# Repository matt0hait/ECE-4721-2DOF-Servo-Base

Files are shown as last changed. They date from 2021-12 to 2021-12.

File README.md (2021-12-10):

# ECE-4721 2 DOF Servo Base

by Matthew Hait

## Introduction

This project is for ECE-4721 Embedded Systems at Oakland University. It features two degrees of freedom, 5 MOA accuracy on each axis, and a minimum speed of 60 RPM for all accceptable end of arm tooling loads.

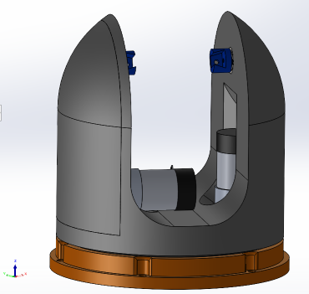
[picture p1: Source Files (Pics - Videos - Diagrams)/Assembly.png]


## Components
- FRDM-KL25Z
- Hall-Effect Sensors
- Motors
- L298N Motor Controller

## License

[MIT](LICENSE)

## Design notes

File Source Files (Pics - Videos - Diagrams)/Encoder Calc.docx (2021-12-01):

From motor datasheet:

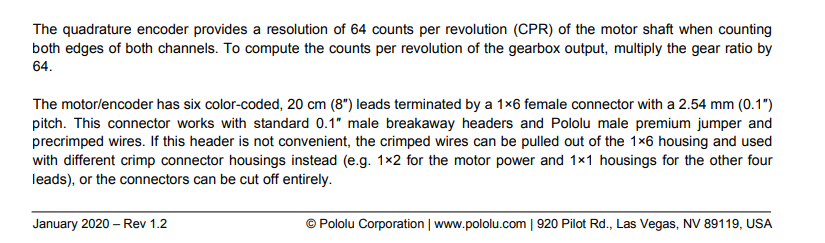
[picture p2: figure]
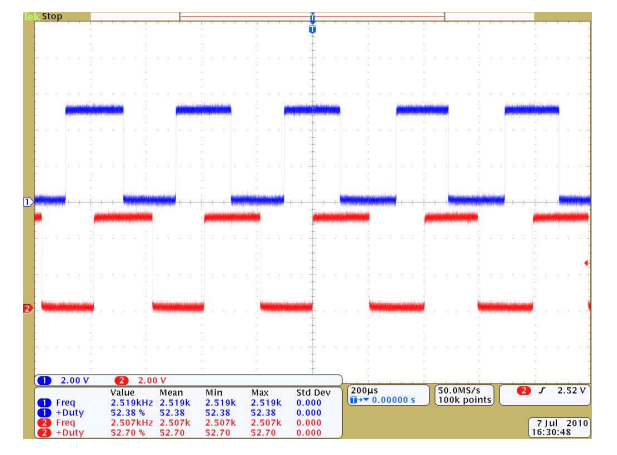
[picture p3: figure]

E.g.

- 64 counts in rising and falling edge of both channels
- 32 counts rising edge channel one + falling edge channel 2 (180 out of phase)
- 16 counts in rising edge of one channel

Rising Edge one channel:

(1 Rev_M)/(16 pulse)* (1 Rev_G)/(10 Rev_M)*(15 teeth)/(1 Rev_G)*(1 Rev_O)/(100 teeth)*(360°)/(1 Rev_O)=0.3375 °/pulse

Rising Edge channel one + falling edge channel 2 (180 out of phase):

(1 Rev_M)/(32 pulse)* (1 Rev_G)/(10 Rev_M)*(15 teeth)/(1 Rev_G)*(1 Rev_O)/(100 teeth)*(360°)/(1 Rev_O)=0.16875 °/pulse

Rising and falling edge of both channels

(1 Rev_M)/(64 pulse)* (1 Rev_G)/(10 Rev_M)*(15 teeth)/(1 Rev_G)*(1 Rev_O)/(100 teeth)*(360°)/(1 Rev_O)=0.084375 °/pulse

- RevM: Revolution of motor shaft
- RevG: Revolution of gearbox output
- RevO: Revolution of outer gear

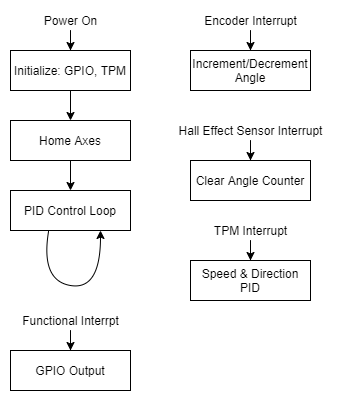
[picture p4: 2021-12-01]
Source Files (Pics - Videos - Diagrams)/ECE-4721 Final Project-Flow.drawio.png

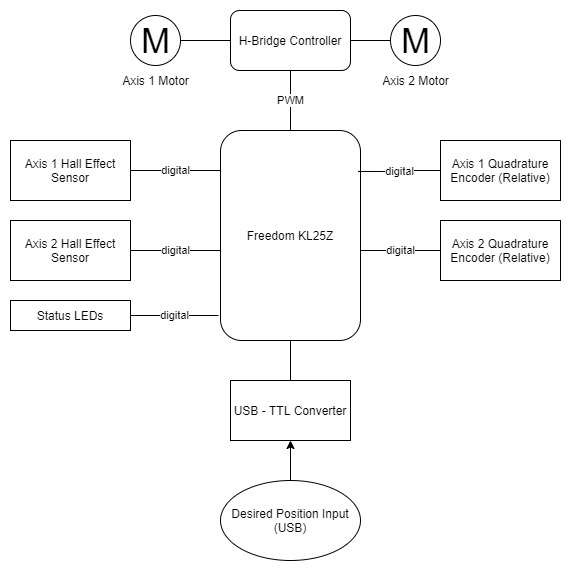
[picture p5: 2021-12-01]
Source Files (Pics - Videos - Diagrams)/ECE-4721-Final-Project.jpg

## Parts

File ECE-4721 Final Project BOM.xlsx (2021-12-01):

Desc | PN | Cost | QTY | Total | Notes
Axis 1 Slip Ring | SRC012C | $14.95 | 1 | $14.95 | https://www.mouser.com/ProductDetail/Adafruit/736?qs=GURawfaeGuDEdKB7mAhcWw%3D%3D
Axis 2 Bearing | 2342K165 | $15.00 | 2 | $30.00 | https://www.mcmaster.com/2342K165/
Axis 2 Motor | 4755 | $39.95 | 1 | $39.95 | https://www.pololu.com/product/4755
Axis 2 Pulley | B08P6KVQLD | $2.96 | 2 | $5.93 | https://www.amazon.com/Taiss-Printer-Aluminum-Included-F020-W-7/dp/B08P6KVQLD?s=industrial
Axis 2 Idler Pulley | B07RV2T54M | $1.20 | 1 | $1.20 | https://www.amazon.com/dp/B07RV2T54M?ref=ppx_yo2_dt_b_product_details&th=1
Axis 2 Belt | LXMY1538 | $3.50 | 1 | $3.50 | https://www.amazon.com/dp/B07RK1TX8C?psc=1&ref=ppx_yo2_dt_b_product_details
Axis 2 Slip Ring | 485-775 | $17.50 | 1 | $17.50 | https://www.mouser.com/ProductDetail/Adafruit/775?qs=GURawfaeGuCCOTAoJcRDEQ%3D%3D
Axis 1 Bearing | 5972K115 | $22.66 | 1 | $22.66 | https://www.mcmaster.com/5972K115/
Axis 1 Motor | 4758 | $39.95 | 1 | $39.95 | https://www.pololu.com/product/4758
Axis 1 Thurst Bearings | 9613K52 | $0.47 | 60 | $27.94 | https://www.mcmaster.com/9613K52/
Motor Gear | 2664N506 | $0.20 | 0 | $0.00 | https://www.mcmaster.com/catalog/2664n506 3D Print or buy
Motor controller | L298N | $6.99 | 1 | $6.99 | https://www.amazon.com/Qunqi-Controller-Module-Stepper-Arduino/dp/B014KMHSW6?s=industrial
Power Supply | 2882-15DYS902-120750G-ND | $30.03 | 1 | $30.03 | https://www.digikey.com/en/products/detail/ideal-power-ltd/15DYS902-120750G/12818209
1lg PLA Filament | B01EKEMDA6 | $22.99 | 1 | $22.99 | https://www.amazon.com/eSUN-1-75mm-Printer-Filament-2-2lbs/dp/B01EKEMDA6
Microcontroller | FRDM-KL25Z | $19.12 | 1 | $19.12 | https://www.amazon.com/NXP-SEMICONDUCTOR-FRDM-KL25Z-Development-Platform/dp/B073RQ5CTK?s=industrial
Total: |  |  |  | $282.70

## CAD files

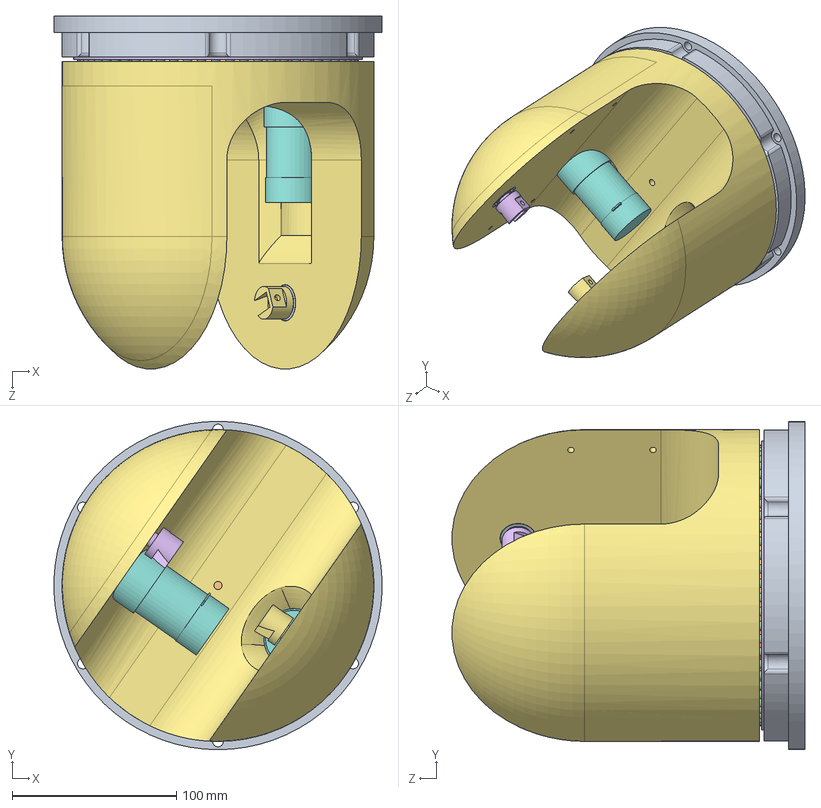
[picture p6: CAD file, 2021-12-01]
CAD/Servo_Base.SLDASM
199.8 x 200.0 x 214.8 mm
Servo_Base
SRC022-6_Slip_Ring
5972K115_Ball Bearing
6mm_BB x 60
2664N506_Metal Gear - 20 Degree Pressure Angle
Thrust_Bearing_Race_Way
Servo_Turret
Pololu 4758 Motor x 2
2342K165_Permanently Lubricated Ball Bearing x 2
B08P6KVQLD Belt Pulley x 2
GT2_Idler_Pully
Idler Tensioner
Belt2-6^Servo_Base
Axis_2_Mount
Axis_2_Mount-B
Slip_Ring_775

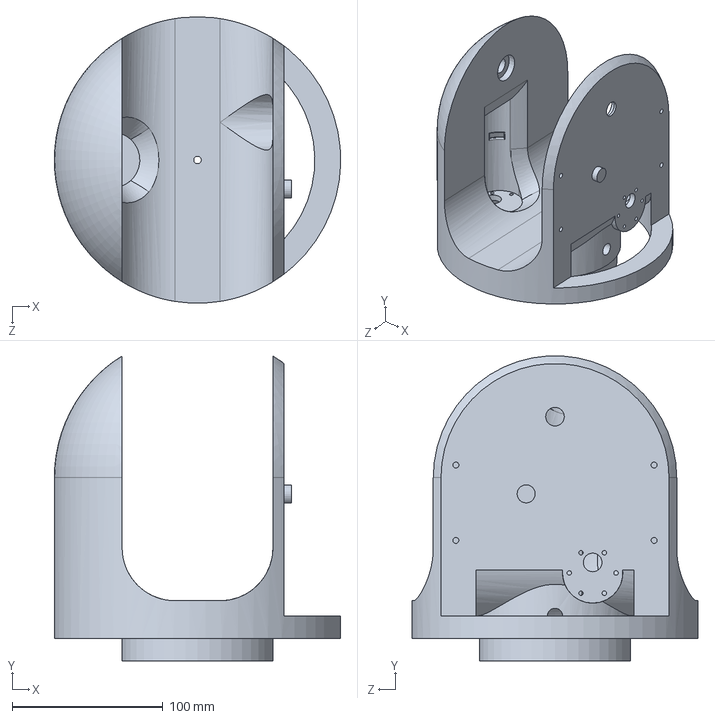
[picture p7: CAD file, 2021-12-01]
CAD/Servo_Turret.SLDPRT
190.0 x 202.3 x 190.0 mm

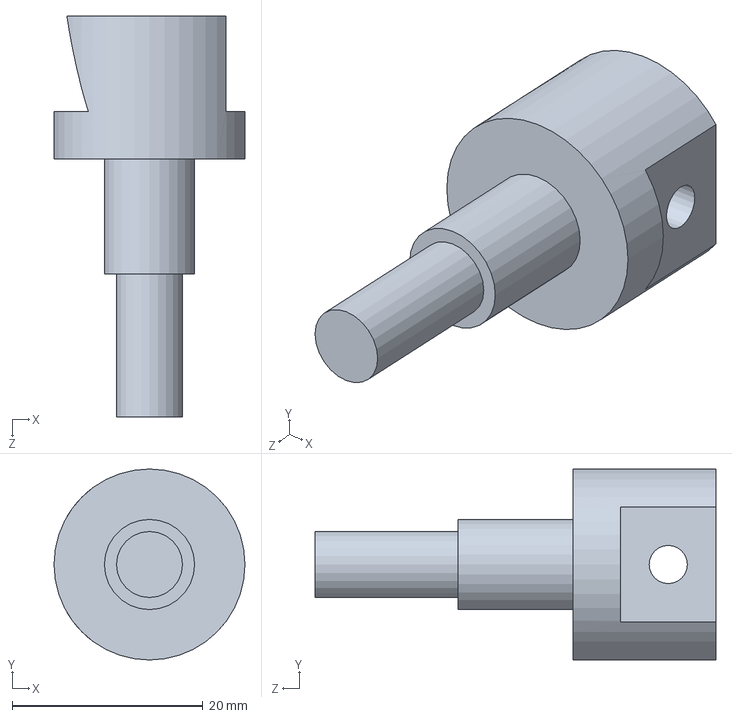
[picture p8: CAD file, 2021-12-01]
CAD/Axis_2_Mount.SLDPRT
20.0 x 20.0 x 42.0 mm

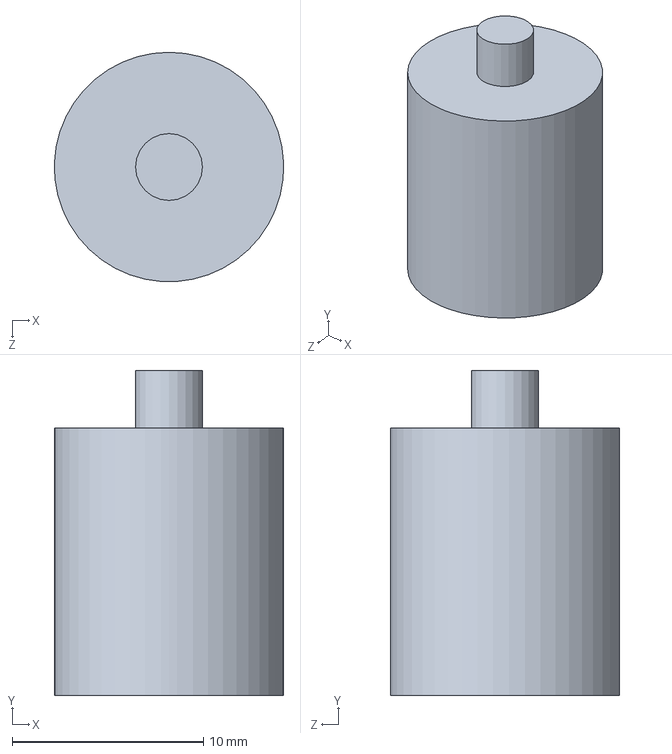
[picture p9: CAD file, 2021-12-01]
CAD/Slip_Ring_775.SLDPRT
12.0 x 17.0 x 12.0 mm

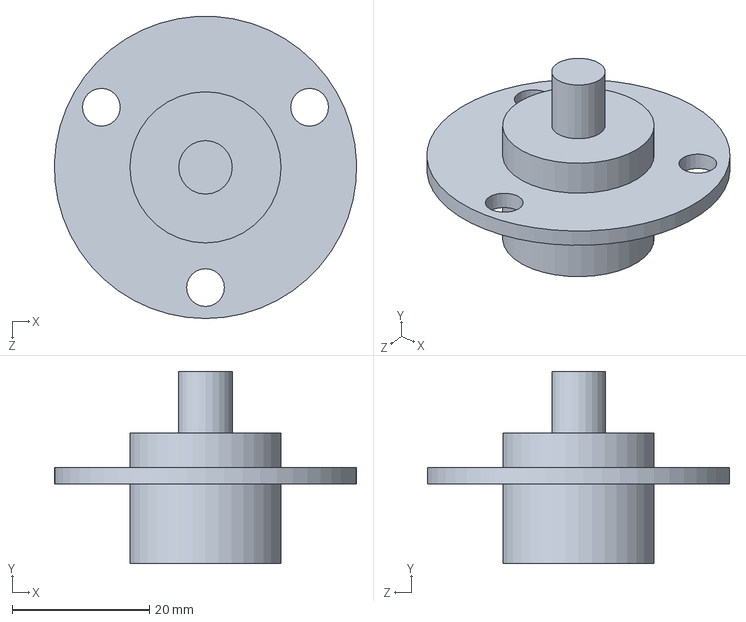
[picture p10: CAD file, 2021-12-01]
CAD/SRC022-6_Slip_Ring.SLDPRT
44.0 x 28.0 x 44.0 mm

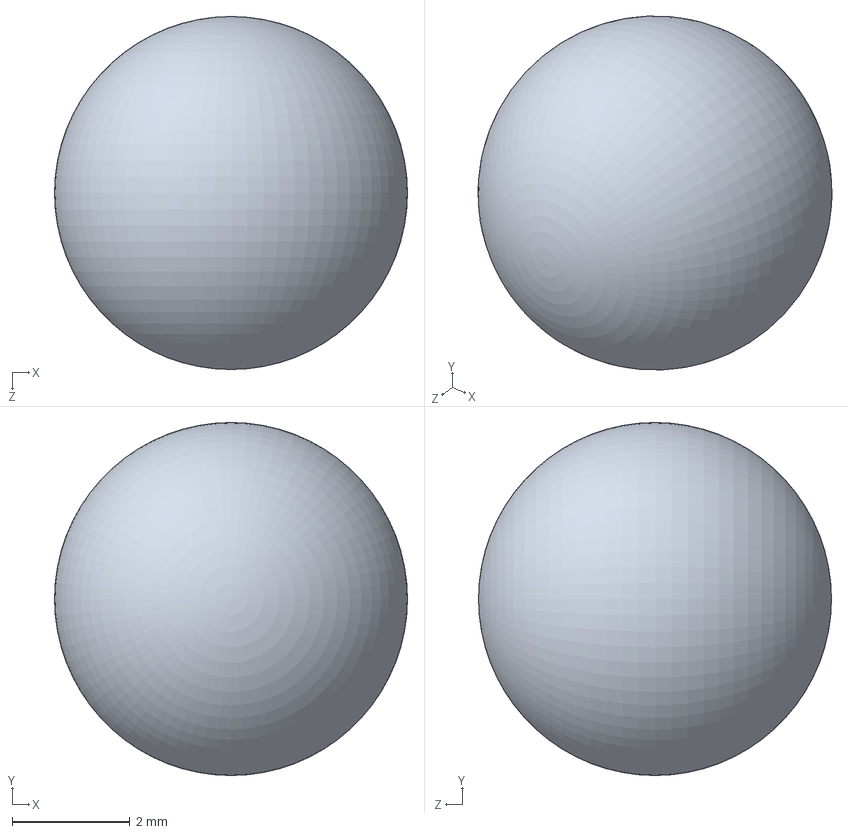
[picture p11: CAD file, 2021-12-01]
CAD/6mm_BB.SLDPRT
6.00 x 6.00 x 6.00 mm

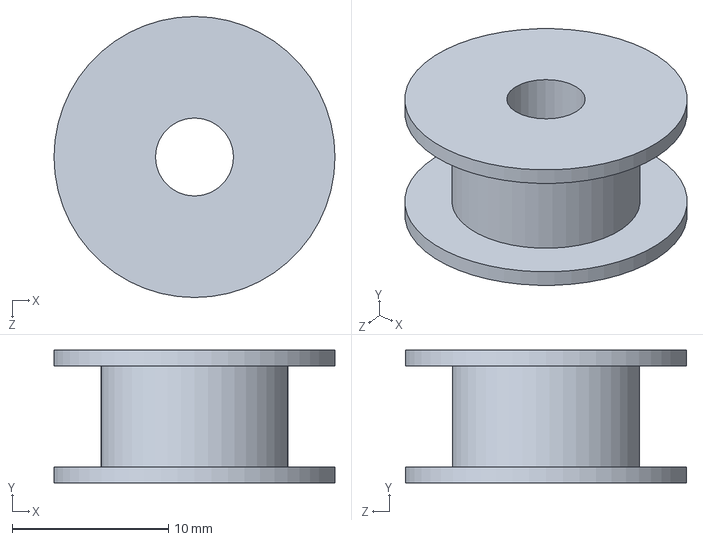
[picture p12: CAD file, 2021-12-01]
CAD/GT2_Idler_Pully.SLDPRT
18.0 x 8.50 x 18.0 mm

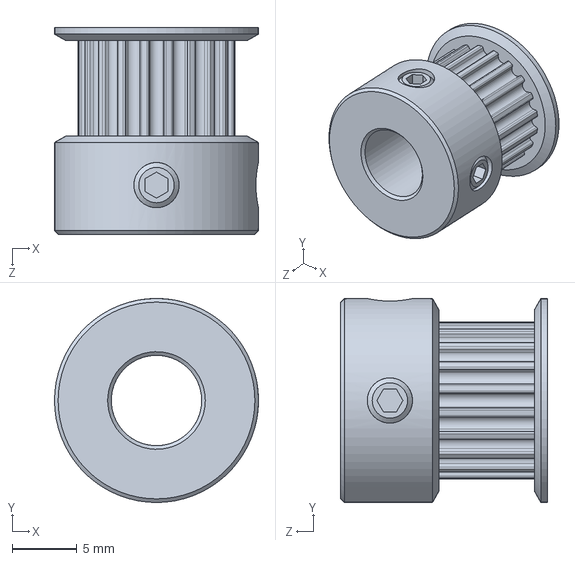
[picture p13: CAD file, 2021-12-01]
CAD/B08P6KVQLD Belt Pulley.SLDPRT
15.8 x 15.8 x 16.0 mm

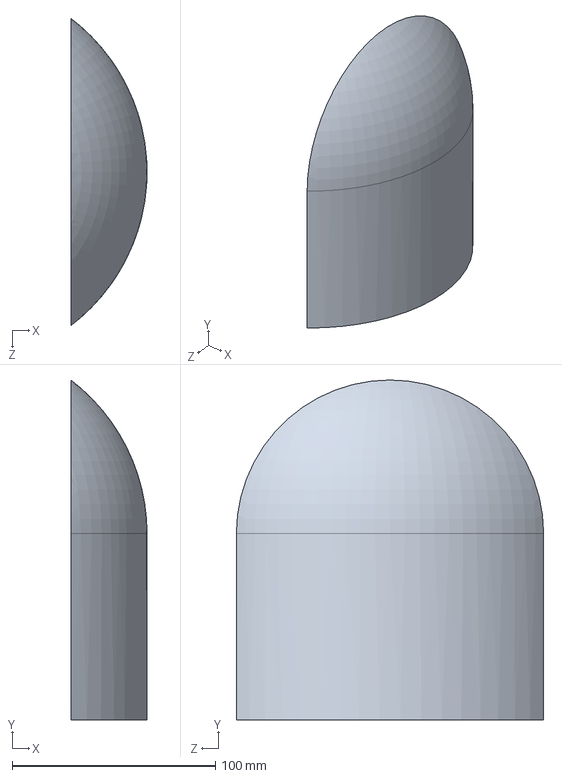
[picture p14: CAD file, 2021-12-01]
CAD/Body2.SLDPRT
37.5 x 167.3 x 151.2 mm

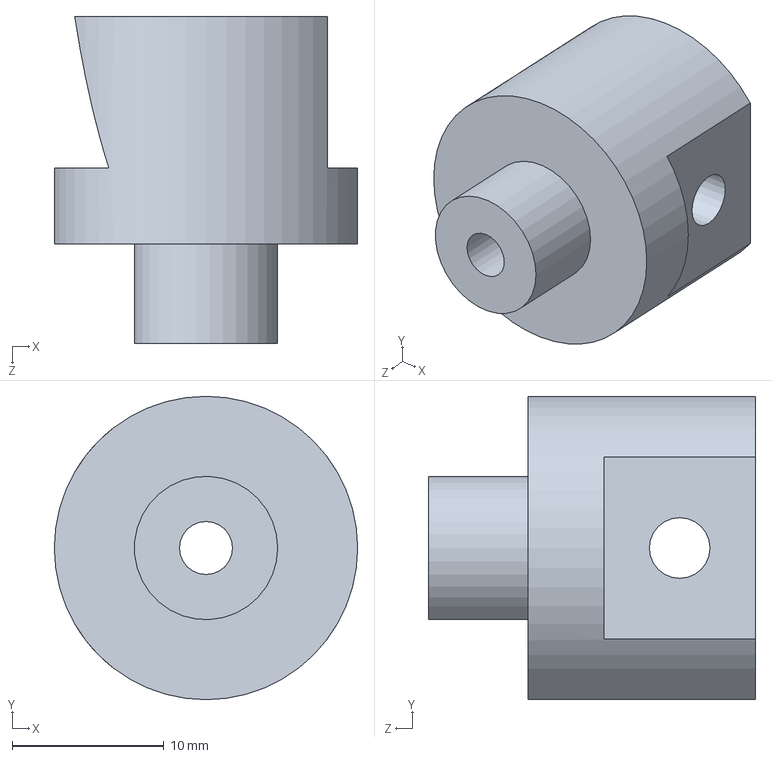
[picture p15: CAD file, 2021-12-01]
CAD/Axis_2_Mount-B.SLDPRT
20.0 x 20.0 x 21.6 mm

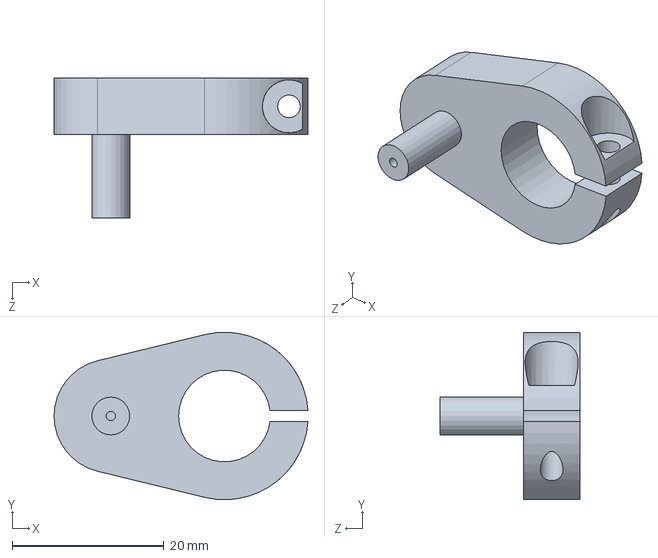
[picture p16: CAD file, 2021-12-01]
CAD/Idler Tensioner.SLDPRT
33.5 x 22.1 x 18.5 mm

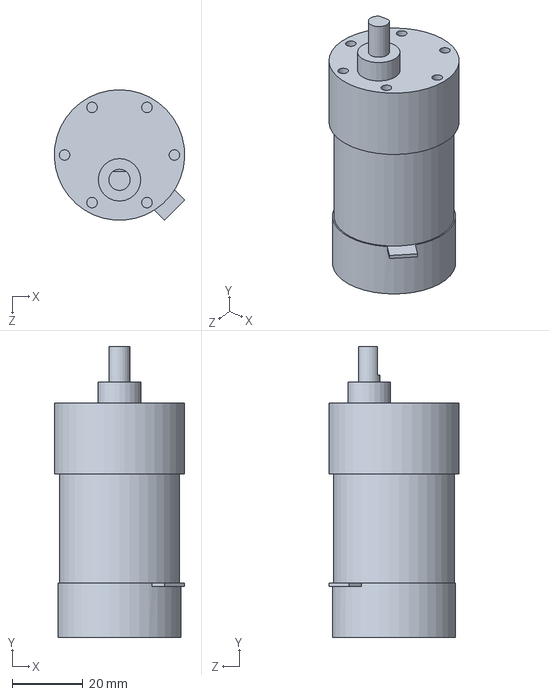
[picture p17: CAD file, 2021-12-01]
CAD/Pololu 4758 Motor.SLDPRT
36.8 x 82.1 x 36.8 mm

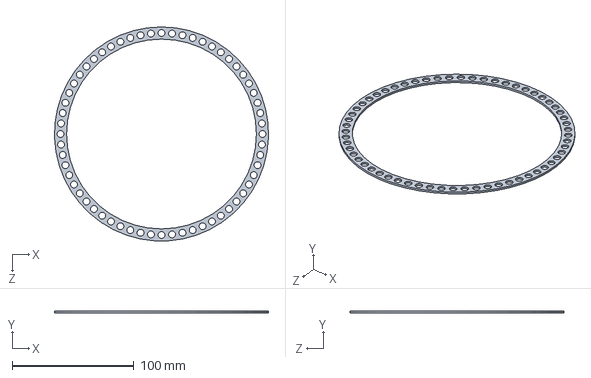
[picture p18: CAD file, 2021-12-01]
CAD/Thrust_Bearing_Race_Way.SLDPRT
176.0 x 1.50 x 176.1 mm

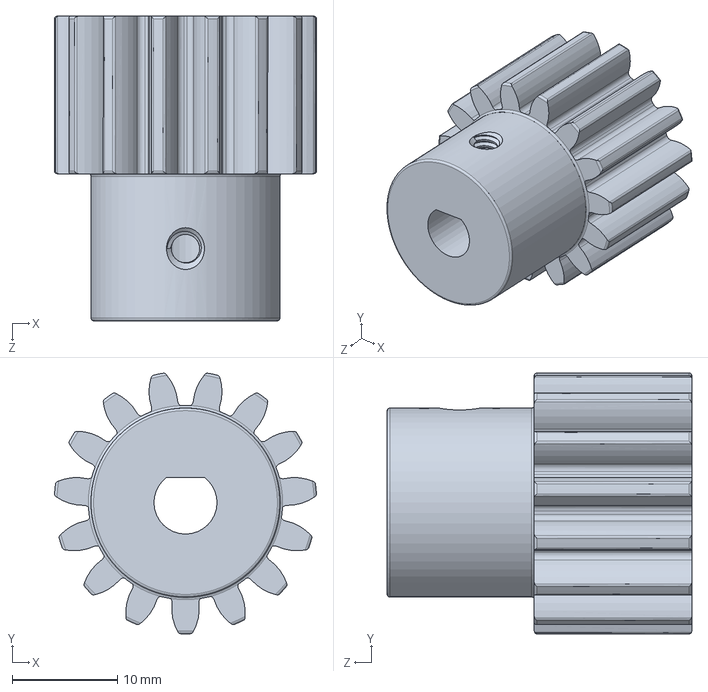
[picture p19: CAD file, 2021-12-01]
CAD/2664N506_Metal Gear - 20 Degree Pressure Angle.SLDPRT
24.9 x 24.8 x 29.0 mm

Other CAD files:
CAD/Body1.SLDPRT
CAD/5972K115_Ball Bearing.SLDPRT
CAD/2342K165_Permanently Lubricated Ball Bearing.SLDPRT
CAD/Servo_Base.SLDPRT

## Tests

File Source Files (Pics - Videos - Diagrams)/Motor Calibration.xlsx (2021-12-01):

Axis 1 Motor Calibration @ 12V |  |  |  | Pulses/Rev:
PWM input | Pulse / Sec | RPS | deg/s | Axis 1 | 4267
0 | 0 | 0 | 0 | Axis 2 | 6533
4800 | 0 | 0 | 0
9600 | 0 | 0 | 0
14400 | 1030 | 0.2413873916 | 86.89946098
19200 | 3360 | 0.7874384814 | 283.4778533
24000 | 5060 | 1.185844856 | 426.9041481
28800 | 6200 | 1.453011483 | 523.0841341
33600 | 7300 | 1.710803843 | 615.8893836
38400 | 7860 | 1.84204359 | 663.1356925
43200 | 8320 | 1.949847668 | 701.9451605
48000 | 9160 | 2.146707288 | 772.8146239
Axis 2 Motor Calibration @ 12V
PWM input | Pulse / Sec | RPS | deg/s
0 | 0 | 0 | 0
4800 | 0 | 0 | 0
9600 | 3680 | 0.5632940456 | 202.7858564
14400 | 6590 | 1.008724935 | 363.1409766
19200 | 8090 | 1.238328486 | 445.798255
24000 | 8990 | 1.376090617 | 495.3926221
28800 | 9590 | 1.467932037 | 528.4555334
33600 | 9890 | 1.513852748 | 544.9869891
38400 | 10180 | 1.558242767 | 560.9673963
43200 | 10350 | 1.584264503 | 570.3352212
48000 | 10780 | 1.650084188 | 594.0303077
 |  |  |  |  |  | s

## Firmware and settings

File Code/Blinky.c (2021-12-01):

/* 	Matthew Hait
		ECE 4721
		F 2021
		Final Project */
		
#include "MKL25Z4.h"
#include <stdbool.h>
#include <string.h>
#include <math.h>
 
#define MASK(x) (1UL << (x))
#define DOF		2							// @brief Degrees of Freedom
#define PWM_PERIOD (48000) 	// @brief Period of PWM
#define F_TPM_CLOCK 48000000// @brief Running frequency of the MCU [Hz]
#define F_TPM_OVFLW	250			// @brief Frequency to run TP2 interrupt [Hz]
#define TPM2_PERIOD	4000		// @brief Frequency to run TP2 interrupt [us]

// PID Constants
#define tau  8000

// Encoder Inputs 		(PORT A):
#define AXIS_1_ENC_A		1		// @brief Port A1
#define AXIS_1_ENC_B		2		// @brief Port A2
#define AXIS_2_ENC_A		4		// @brief Port A4
#define AXIS_2_ENC_B		12	// @brief Port A12

// Hall Effect Inputs	(PORT D):
#define AXIS_1_HALL			1		// @brief Port D1
#define AXIS_2_HALL			2		// @brief Port D2

// Motor Outputs			(PORT B):
#define AXIS_1_MTR_A		2 		// @brief Port B2
#define AXIS_1_MTR_B		1 		// @brief Port B1
#define AXIS_2_MTR_A		3 		// @brief Port B3
#define AXIS_2_MTR_B		8 		// @brief Port B8

// Motor Speeds				(PORT C):
#define AXIS_1_MTR_PWM	2	 		// @brief TPM 0.1
#define AXIS_2_MTR_PWM	8 		// @brief TPM 0.4

// Functional Outputs
#define STATUS_LED			1 		// @brief D1
#define OPT_CONTROL			2 		// @brief TBD

// @brief Structure for storing axis logic
struct axis {
	uint32_t	Motor_A;				// Motor Input Direction Pin A
	uint32_t	Motor_B;				// Motor Input Direction Pin B
	uint32_t	hall_sense;			// Hall Effect Sensor Pin A
    // @brief Quadrature Encoder values for calculating steps
	struct		encoder {
		uint32_t	Encoder_A;			// Encoder Input Pin A
		uint32_t	Encoder_B;			// Encoder Input Pin B
		bool			old_b;					// Encoder B previous state
		bool			old_a;					// Encoder A previous state
		bool			new_a;					// Encoder A current state
		bool			new_b;					// Encoder B current state
		size_t		old_count;			// Old count from home
		size_t		new_count;			// Current count from home
		size_t		backlash;				// Encoder counts from center of home to the edge of area of effect
	} encoder;
	struct		PID {
		float		KP;								// Proportional Gain
		float		KI;								// Integral Gain
		float		KD;								// Derivative Gain
		float		p_error;					// Previous Error
		float		integrator;				// PID integrating error
		float		differentiator;		// PID differential error
		float		PID_LIM_MIN;			// Max Negative Jerk [deg/sec]
		float		PID_LIM_MAX;			// Max Jerk [deg/sec]
		float		PID_LIM_MIN_INT;	// Max Initial Negative Jerk [deg/sec]
		float		PID_LIM_MAX_INT;	// Max Initial Jerk [deg/sec]
	} PID;
	struct		PWM{
		uint32_t	PWM;						// Motor PWM Pin A
		uint8_t		TPM_CH;					// TPM CH
		uint8_t		TPM_ALT;					// TPM Alt Number
		size_t		Pulse_Per_Rev;	// Encoder counts per 360 deg
		float		deg_per_pulse;		// Deg per encoder count
		float		v_b;							// 2rd Deg poly: b
		float		v_x1;							// 2rd Deg poly: x
		float		v_x2;							// 2rd Deg poly: x^2
	} PWM;
	bool		calibrated;				// Calibrate from home point
	float		velocity;					// [Deg per second]
	float		p_velocity;				// Previous Vel [Deg per second] (For PID)
  float		target_velocity;	// Deg per second
};

struct axis dof_axes[DOF];	// @brief Array of DOF Axes
const int enc_LUT[16] = {0, -1, 1, 2, 1, 0, 2, -1, -1, 2, 0, 1, 2, 1, -1, 0}; // @brief Lookup table for encoder step from interrupts
uint8_t PORTD_ISR_Mode = 0; // @brief Controls what the PORTD interrupt does

	
void motor_control(struct axis* inAxis, bool clockwise, bool brake, uint16_t PWM_Duty);

/* @brief	Calculates angular velocity [deg/sec] from step count traversed over a period of sample time.
 *          Sets velocity value in axis structure.
 * @param		inAxis      Axis to calculate
 * @param		sample_time  Time between old_count and new_count [us] */
void calculate_speed(size_t i, size_t sample_time) {
		dof_axes[i].p_velocity = dof_axes[i].velocity;	//Pass old velocity
    dof_axes[i].velocity = (((float)dof_axes[i].encoder.new_count - (float)(dof_axes[i].encoder.old_count)) * dof_axes[i].PWM.deg_per_pulse) / (float)sample_time;
    dof_axes[i].velocity *= 1000000;   // Convert us to s
    dof_axes[i].encoder.old_count = dof_axes[i].encoder.new_count; // NOTE: Updating count HERE. IMPORTANT!!!
}

void Delay(volatile unsigned int time_del) {
	while (time_del--) {
		;
	}
}

/* @brief	Rotate Axis to home and calculate offsets
 *			Can only home one axis at a time. While homing, home detection for other axes is halted.
 * @param	inAxis	Axis to locate home */
void home_axis(struct axis* inAxis) {
	// TODO: Use goto_motor_control_function instead
	PORTD_ISR_Mode = 0;	// Set PORTD ISR to calibration mode
	// TODO: Set PWM speed below to 20% maximum
	motor_control(inAxis, true, false, 20);
	while(!inAxis->calibrated) {
		;	// Wait until PORTD ISR sets calibration
			// TODO: Add watchdog incase calibration cannot be set
	}
	// TODO: Turn clockwise 10deg, turn counterclockwise until rising edge, calculate backlash
	motor_control(inAxis, false, false, 5);
	while(inAxis->encoder.new_count != 0) {
		;	// Wait until home is reached
			// TODO: Add watchdog
	}
	PORTD_ISR_Mode = 1;	// Set PORTD ISR to normal mode
	// Apply Brake
	PTB->PSOR = MASK(inAxis->Motor_A);
	PTB->PSOR = MASK(inAxis->Motor_A);
}
// @brief Intialize TPM2 Timer for velocity function
void initalize_TPM2() {
	SIM->SCGC6 |= SIM_SCGC6_TPM2_MASK;
	//SIM->SOPT2 |= SIM_SOPT2_TPMSRC(1); // Don't need to do this twice
	TPM2->MOD = (F_TPM_CLOCK/(F_TPM_OVFLW*32))-1;
	TPM2->SC	= TPM_SC_CMOD(1) | TPM_SC_PS(5) | TPM_SC_TOIE_MASK;
	// Run with interrupt
	NVIC_SetPriority(TPM2_IRQn,3);
	NVIC_ClearPendingIRQ(TPM2_IRQn);
	NVIC_EnableIRQ(TPM2_IRQn);
}

// @brief Intialize GPIO
void initalize_GPIO() {
	SystemCoreClockUpdate();
	SysTick_Config(10000);
	struct axis a_axis = {
					.Motor_A = AXIS_1_MTR_A,
					.Motor_B = AXIS_1_MTR_B,
					.hall_sense = AXIS_1_HALL,
					.encoder = {
						.Encoder_A = AXIS_1_ENC_A, 
						.Encoder_B = AXIS_1_ENC_B,
						.old_count = 0,
						.new_count = 0,
						.backlash = 0
					},
					.PID = {
						.KP = 2,
						.KI = 0.5,
						.KD = 0.25,
						.p_error = 0,
						.integrator = 0,
						.differentiator = 0,
						.PID_LIM_MIN = -250,
						.PID_LIM_MAX = 250,
						.PID_LIM_MIN_INT = -100,
						.PID_LIM_MAX_INT = 100
					},
					.PWM = {
						.PWM = AXIS_1_MTR_PWM,
						.TPM_CH = 1,
						.TPM_ALT = 4,
						.Pulse_Per_Rev = 4267,
						.deg_per_pulse = 0.084375,
						.v_b = 3579.8,
						.v_x1 = -34.371,
						.v_x2 = 0.1704
					},
					.calibrated = false,
					.velocity = 0,
					.p_velocity = 0
				};
	struct axis b_axis = {
					.Motor_A = AXIS_2_MTR_A,
					.Motor_B = AXIS_2_MTR_B,
					.hall_sense = AXIS_2_HALL,
					.encoder = {
						.Encoder_A = AXIS_2_ENC_A, 
						.Encoder_B = AXIS_2_ENC_B,
						.old_count = 0,
						.new_count = 0,
						.backlash = 0
					},
					.PID = {
						.KP = 2,
						.KI = 0.75,
						.KD = 3,
						.p_error = 0,
						.integrator = 0,
						.differentiator = 0,
						.PID_LIM_MIN = -250,
						.PID_LIM_MAX = 250,
						.PID_LIM_MIN_INT = -100,
						.PID_LIM_MAX_INT = 100
					},
					.PWM = {
						.PWM = AXIS_2_MTR_PWM,
						.TPM_CH = 4,
						.TPM_ALT = 3,
						.Pulse_Per_Rev = 6533,
						.deg_per_pulse = 0.055103,
						.v_b = 6215.6,
						.v_x1 = 33.121,
						.v_x2 = 0.0247
					},
					.calibrated = false,
					.velocity = 0,
					.p_velocity = 0
				};
	struct axis temp_dof_axes[DOF] = {a_axis, b_axis}; 				// Declare here for clean look
	memcpy(dof_axes, temp_dof_axes, sizeof(temp_dof_axes));		// Copy to global variable (compiler should remove this from code)
	// Setup Clock PLL
	MCG->C1 |= MCG_C1_CLKS(0);  // Select PLL/FLL as clock source
	MCG->C1 |= MCG_C1_IREFS(1); // Select Inernal Reference clock
	MCG->C4 |= MCG_C4_DRST_DRS(1); // Select DCO range as Mid range
	MCG->C4 |= MCG_C4_DMX32(1);    // Select DCO frequency as 48Mhz
	// Initalize Port Clocks:
	SIM->SCGC5 |= SIM_SCGC5_PORTA_MASK;												// Enable clock on Port A
	SIM->SCGC5 |= SIM_SCGC5_PORTB_MASK;												// Enable clock on Port B
	SIM->SCGC5 |= SIM_SCGC5_PORTC_MASK;												// Enable clock on Port C
	SIM->SCGC5 |= SIM_SCGC5_PORTD_MASK;												// Enable clock on Port D
	// Initalize TPMs:
	SIM->SCGC6 |= SIM_SCGC6_TPM0_MASK;												// Enable clock on TPM0
	// Configure TPM clocks
	//SIM->SOPT2 |= (SIM_SOPT2_TPMSRC(1) | SIM_SOPT2_PLLFLLSEL_MASK);	// Set TPM input freq to 48 MHz // Alexander G. Dean is an idiot.
	SIM->SOPT2 |= SIM_SOPT2_TPMSRC(1);
	TPM0->MOD = PWM_PERIOD-1;						// Load the counter and MOD
	TPM0->SC = TPM_SC_PS(1);						// Set TPM count direction and prescale
	//TPM0->CONF |= TPM_CONF_DBGMODE(3);	// Continue in debug mode // TODO: Is this needed?
	// Initalize Axes GPIO
	for (size_t i = 0; i < DOF; i++) {
		// All motor directions must be on PORTB
		PORTB->PCR[dof_axes[i].Motor_A] &= ~PORT_PCR_MUX_MASK;
		PORTB->PCR[dof_axes[i].Motor_A] |= PORT_PCR_MUX(1);
		PORTB->PCR[dof_axes[i].Motor_B] &= ~PORT_PCR_MUX_MASK;
		PORTB->PCR[dof_axes[i].Motor_B] |= PORT_PCR_MUX(1);
		// All encoders must be on PORTA
		PORTA->PCR[dof_axes[i].encoder.Encoder_A] &= ~PORT_PCR_MUX_MASK;
		PORTA->PCR[dof_axes[i].encoder.Encoder_A] |= PORT_PCR_MUX(1);
		PORTA->PCR[dof_axes[i].encoder.Encoder_A] |= PORT_PCR_IRQC(11);	// Interrupt on rising and falling edge
		PORTA->PCR[dof_axes[i].encoder.Encoder_B] &= ~PORT_PCR_MUX_MASK;
		PORTA->PCR[dof_axes[i].encoder.Encoder_B] |= PORT_PCR_MUX(1);
		PORTA->PCR[dof_axes[i].encoder.Encoder_B] |= PORT_PCR_IRQC(11);	// Interrupt on rising and falling edge
		// All hall-effect sensors must be on PORTD
		PORTD->PCR[dof_axes[i].hall_sense] &= ~PORT_PCR_MUX_MASK;
		PORTD->PCR[dof_axes[i].hall_sense] |= PORT_PCR_MUX(1);
		PORTD->PCR[dof_axes[i].hall_sense] |= PORT_PCR_IRQC(0x0B);	// Interrupt on rising and falling edge
		PORTD->PCR[STATUS_LED] &= ~PORT_PCR_MUX_MASK;
		PORTD->PCR[STATUS_LED] |= PORT_PCR_MUX(1);
		// All PWM must be on PORTC
		// L298N H bridge accepts up to 40 kHz PWM frequency
		PORTC->PCR[dof_axes[i].PWM.PWM] &= ~PORT_PCR_MUX_MASK;
		PORTC->PCR[dof_axes[i].PWM.PWM] |= PORT_PCR_MUX(dof_axes[i].PWM.TPM_ALT); // Alt# changes between pins
		// Set Outputs
		PTB->PDDR |= MASK(dof_axes[i].Motor_A) | MASK(dof_axes[i].Motor_B);
		// Set Inputs
		PTA->PDDR &= ~(MASK(dof_axes[i].encoder.Encoder_A) | MASK(dof_axes[i].encoder.Encoder_B));
		PTD->PDDR &= ~MASK(dof_axes[i].hall_sense);
		PTD->PDDR |= MASK(STATUS_LED);
		// Apply brakes on startup
		PTB->PSOR = MASK(dof_axes[i].Motor_A);
		PTB->PSOR = MASK(dof_axes[i].Motor_B);
		// Grab current encoder value
		dof_axes[i].encoder.old_a = PTA->PDIR & MASK(dof_axes[i].encoder.Encoder_A);
		dof_axes[i].encoder.old_b = PTA->PDIR & MASK(dof_axes[i].encoder.Encoder_B);
		// Configure TPM channels
		//TPM0->CONTROLS[dof_axes[i].TPM_CH].CnSC = TPM_CnSC_MSB_MASK | TPM_CnSC_ELSA_MASK;	// Set CH of TPM0 to edge-aligned low-true PWM
		TPM0->CONTROLS[dof_axes[i].PWM.TPM_CH].CnSC = (TPM_CnSC_ELSB(1) | TPM_CnSC_ELSA(0) | TPM_CnSC_MSB(1)  | TPM_CnSC_MSA(0));
		TPM0->CONTROLS[dof_axes[i].PWM.TPM_CH].CnV = 0;					// Set initial speed to 0;
		TPM0->SC |= TPM_SC_CMOD(dof_axes[i].PWM.TPM_CH);					// Start TPM0
	}
	// Enable interrupts for encoders
	NVIC_SetPriority(PORTA_IRQn, 2);
	NVIC_ClearPendingIRQ(PORTA_IRQn);
	NVIC_EnableIRQ(PORTA_IRQn);
	// Enable interrupts for hall effect sensor
	NVIC_SetPriority(PORTD_IRQn, 3);
	NVIC_ClearPendingIRQ(PORTD_IRQn);
	//NVIC_EnableIRQ(PORTD_IRQn);
	PTD->PSOR = MASK(STATUS_LED);
}

void motor_control(struct axis* inAxis, bool clockwise, bool brake, uint16_t PWM_Duty) {
	// Short motor windings for hard brake
	if (brake) {
		PTB->PSOR = MASK(inAxis->Motor_A);
		PTB->PSOR = MASK(inAxis->Motor_B);		
		TPM0->CONTROLS[inAxis->PWM.TPM_CH].CnV = 0;
	} else {
		// Output Direction
		// TODO: Check if input direction is different from currently set. Add backlash offset if true.
		if (clockwise) {
			PTB->PCOR = MASK(inAxis->Motor_B);	// Clear first to prevent brake if interrupt occurs after
			PTB->PSOR = MASK(inAxis->Motor_A);
		} else {
			PTB->PCOR = MASK(inAxis->Motor_A);
			PTB->PSOR = MASK(inAxis->Motor_B);
		}
		TPM0->CONTROLS[inAxis->PWM.TPM_CH].CnV = PWM_Duty;
	}
}

// @brief PORTA Interrupt Handler (Encoder Inputs)
void PORTA_IRQHandler(void) {
	//DEBUG_PORT->PSOR = MASK(DBG_ISR_POS); // Is this needed?
	PTD->PCOR = MASK(STATUS_LED);
	size_t i = 0;
	// Loop through axes and set new input
	for ( ; i < DOF; i++) {
		// Check A of encoder
		if (PORTA->ISFR & MASK(dof_axes[i].encoder.Encoder_A)) {
			dof_axes[i].encoder.new_a = PTA->PDIR & MASK(dof_axes[i].encoder.Encoder_A);
			break;	// Exit, no need to iterate through rest of axes.
		}
		// Check B of encoder
		if (PORTA->ISFR & MASK(dof_axes[i].encoder.Encoder_B)) {
			dof_axes[i].encoder.new_b = PTA->PDIR & MASK(dof_axes[i].encoder.Encoder_B);
			break;
		}
	}
	// Calculate count of interrupt axis
	int old_sum = (dof_axes[i].encoder.old_a << 1) + dof_axes[i].encoder.old_b;
	int new_sum = (dof_axes[i].encoder.new_a << 1) + dof_axes[i].encoder.new_b;
	dof_axes[i].encoder.new_count +=  enc_LUT[old_sum*4+new_sum];
	// TODO: Check if LUT = 2 (encoder skipped a step) then reboot, rehome, or count errors.
	// Check for count overflows
	if(dof_axes[i].encoder.new_count > dof_axes[i].PWM.Pulse_Per_Rev) {
		// Axis has completed a full revolution; reset count
		dof_axes[i].encoder.new_count = 0;
	}
	if(dof_axes[i].encoder.new_count == ((size_t)-1)) {
		// Axis has turned past 0, rest count to max-1
		dof_axes[i].encoder.new_count = dof_axes[i].PWM.Pulse_Per_Rev;
	}
	// Update old values for next interrupt
	dof_axes[i].encoder.old_a = dof_axes[i].encoder.new_a;
	dof_axes[i].encoder.old_b = dof_axes[i].encoder.new_b;
	// clear status flags
	PORTA->ISFR = 0xffffffff;
	//DEBUG_PORT->PCOR = MASK(DBG_ISR_POS); // Need this?
	PTD->PSOR = MASK(STATUS_LED);		
}

// @brief PORTD Interrupt Handler (Hall Effect Sensors)
void PORTD_IRQHandler(void) {
	if (PORTD_ISR_Mode == 0) {
		// Uncalibrated mode
		bool hit_rising_edge = false;
		// Loop through axes and set new input
		size_t i = 0;
		for ( ; i < DOF; i++) {
			if (PORTD->ISFR & MASK(dof_axes[i].hall_sense)) {
				break;	// Exit, no need to iterate through rest of axes.
			}
		}
		// Check for rising edge case
		if (PTD->PDIR & MASK(dof_axes[i].hall_sense)) {
			dof_axes[i].encoder.new_count = 0;
			hit_rising_edge = true;
			return;
		}
		// Check for falling edge case after traveling through home
		if (!(PTD->PDIR & MASK(dof_axes[i].hall_sense) && hit_rising_edge)) {
			dof_axes[i].encoder.new_count /= 2;		// Divide by 2 to grab center of area of effect
			dof_axes[i].calibrated = true;
			return;
		}
		return; // Return to catch rising edge case without traveling through home
	}
	if (PORTD_ISR_Mode == 1) {
		// Normal calibrated operation
	}
	PORTD ->ISFR = 0xffffffff;
}


void speed_PID(size_t i);
// @brief TPM2 Interrupt Handler for measuring velocity
void TPM2_IRQHandler() {
	//`	PTD->PCOR = MASK(STATUS_LED);
	TPM2->SC |= TPM_SC_TOIE_MASK; // Reset overflow flag
	// Calculate vel for all axes
	for (size_t i = 0; i < DOF; i++) {
		//calculate_speed(i, TPM2_PERIOD);
		speed_PID(i);
	}
	//PTD->PSOR = MASK(STATUS_LED);
}

void speed_PID(size_t i) {
		// Thank you pms67: https://github.com/pms67/PID
    calculate_speed(i, TPM2_PERIOD);
    float error = dof_axes[i].target_velocity - dof_axes[i].velocity;
		// P
			float proportional = dof_axes[i].PID.KP * error;
		// I
			dof_axes[i].PID.integrator = dof_axes[i].PID.integrator + 0.5f * dof_axes[i].PID.KI * TPM2_PERIOD * (dof_axes[i].PID.p_error + error);
			// Compute I Limits (Limit the "Limit" on distance away from P
				/*
						float lowILimInt, maxILimInt;
						if (lowILim < proportional) {
							lowILimInt = lowILim - proportional;
						} else {
							lowILimInt = 0.0f;
						}
						if (maxILim > proportional) {
							maxILimInt = maxILim - proportional;
						} else {
							maxILimInt = 0.0f;
						}
			*/
			// Clamp Integrator
			if(dof_axes[i].PID.integrator < dof_axes[i].PID.PID_LIM_MIN_INT) {
				dof_axes[i].PID.integrator = dof_axes[i].PID.PID_LIM_MIN_INT;
			} else if (dof_axes[i].PID.integrator > dof_axes[i].PID.PID_LIM_MAX_INT) {
				dof_axes[i].PID.integrator = dof_axes[i].PID.PID_LIM_MAX_INT;
			}
		// D
			dof_axes[i].PID.differentiator =	-(2.0f * dof_axes[i].PID.KD * (dof_axes[i].velocity - dof_axes[i].p_velocity)
																				+ (2.0f * tau - TPM2_PERIOD) * dof_axes[i].PID.differentiator)
																				/ (2.0f * tau + TPM2_PERIOD);
			
		// P,I,D
			float out = proportional + dof_axes[i].PID.integrator + dof_axes[i].PID.differentiator;
			// Check sign and turn positive if neg. Rotate anti-clkwise if neg.
			bool clk; if(out > 0) { clk = true; } else { clk = false; out *= -1;}
		// Convert [deg/s] => PWM
			size_t PWM_temp = ((out*out)*dof_axes[i].PWM.v_x2) + (out*dof_axes[i].PWM.v_x1) + dof_axes[i].PWM.v_b;
    // Upper Clamp PWM
			 if (PWM_temp > PWM_PERIOD) PWM_temp = PWM_PERIOD;
		// Store
			dof_axes[i].PID.p_error = error;
    // Execute motor control function
			motor_control(&dof_axes[i],clk,false,PWM_temp);
}

int main (void) {
	initalize_GPIO();
	initalize_TPM2();
	// Optional homing function
	//for (size_t i = 0; i < DOF; i++) {
	//	home_axis(&dof_axes[i]);
	//}
	volatile int32_t delay;
	for (;;) {
			float i=0;
			for ( ; i < 594; i+=0.075) {
				dof_axes[0].target_velocity = i;
				dof_axes[1].target_velocity = i;
				Delay(500);
			}
			for ( ; i > 0; i-=0.075) {
				dof_axes[0].target_velocity = i;
				dof_axes[1].target_velocity = i;
				Delay(500);
			}
				Delay(500);
			i=0;
			for ( ; i > -594; i-=0.075) {
				dof_axes[0].target_velocity = i;
				dof_axes[1].target_velocity = i;
				Delay(500);
			}
			for ( ; i < 0; i+=0.075) {
				dof_axes[0].target_velocity = i;
				dof_axes[1].target_velocity = i;
				Delay(500);
			}
				Delay(500);
	}
}
